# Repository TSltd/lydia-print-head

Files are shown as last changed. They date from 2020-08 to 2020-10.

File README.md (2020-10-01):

# lydia-print-head

Lydia-v4 as printhead

***brief*** this is part of our work of PP OpenSource contributions, please check our [library](https://library.precious-plastic.org/) or our [main page](https://plastic-hub.com/products/) for more.

This print head is a modification of [Lydia-v4](https://plastic-hub.com/products/lydia-v4.html) and aims at a generic solution for most of it´s components.

**Status** : Confirmed & in progress, ETA Mid. of October

## Todos

* [x] Hopper interface & lead-out -> Daniel
* [x] Motor selection
* [ ] Firmware updates
  + [x] Check TCP stack memory/CPU footprint on the ControllinoMega
* [x] Sensors / Audio, LED feedback (status, etc... )
* [ ] Bonus : test HMI
* [ ] Support [RAPID - ABB robots, but uses customer spec](https://library.e.abb.com/public/688894b98123f87bc1257cc50044e809/Technical%20reference%20manual_RAPID_3HAC16581-1_revJ_en.pdf)

### Todos Frederike@3dtreehouse

* [ ] Gantry mount plate, we need the size and locations of the mount holes. We'd need a test rig here.
* [x] Modbus over TCP seems a better fit after all which gives us CAT5 shielding as well some standard connectivity. RS485 has no real standard plugs, ...
* [ ] Location and size of the cabinet, what on the control panel (controls & plugs) ?
* [ ] We have to know how we share power source & ground among all digital circuits. Currently we're mostly at 24V and we need another source for 12V (fans, etc...)
* [ ] Clarify RAPID ethernet connectivity

### Todos TimberStar

* [x] we need a laser cut barrel shield which holds the insulation material
* [x] on the barrel tip, we need some mounting possibilties for fans which are a little heavy as well

## Components

* [x] [OMRON MX2 VFD](https://industrial.omron.es/es/products/3G3MX2-A2022-E) [BOM](https://es.wiautomation.com/omron/variadores-motores-proteccion-de-circuitos/3G3MX2A2022E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)
* [x] Controllino - Mega as already mentioned a few times, adds 280 Euro
* [x] a better motor and gearbox - MotoVario
* [ ] custom firmware development
* [x] ModBus capable PID controllers (3x) : [Omron - E5DC-B](https://industrial.omron.eu/en/products/E5DC-QX2ASM-002) - Din - Rail Module [BOM](https://es.wiautomation.com/omron/plc-sistemas/E5DCQX2ASM002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)
* [Hopper - Linear Solenoid](https://uk.farnell.com/guardian-electric/t12x19-c-24d/solenoid-pull-operation-24vdc/dp/1608128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)

### Noah OS Variant

* [x] [PLC/Proxy for Aux, Sensors, Relays, etc... - CP1L-EM40DT1-D](http://www.ia.omron.com/products/family/1916/lineup.html), works well with [Omron NB NB3Q-TW01B](https://es.wiautomation.com/omron/hmi-pc-industriales/NB3QTW01B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)

# Status

* [Firmware](https://github.com/plastic-hub/hydra), in development but mostly done
* Hardware, in re-design

### Specs

* Voltage : 220V|380V
* Max. 120Kg, first rev. might be around 60KG
* Controller cable length around 20 meter
* PID : +/- 5 degc tolerance, alarm/cooling outputs

### Gantry Mount

* the gantry mount should be detached from the head-mount -> adapter plate
* @todo : run static tests
* the tool flange is on p30, ([see also ATI Toolchanger - YuTu](https://www.youtube.com/watch?v=kDP-oofDn4w&feature=youtu.be))

### Firmware

- [-] For now, we base all on Arduino based and existing PlasticHub firmware framework, in particular we will use [Controllino-Mega](https://www.controllino.biz/product/controllino-mega/) which gives us Ethernet and RS485. The board has been proven reliable and robust (ideal for prototyping).
- [-] VFD and PID control is mapped to Serial communication which might accept G-Code
- [x] VFD will be Omron-M2X series since we can use existing code. The VFD also supports Modbus (rather difficult)
- [ ] Internal registers/coils (custom PlasticHub Firmware) to Modbus rep

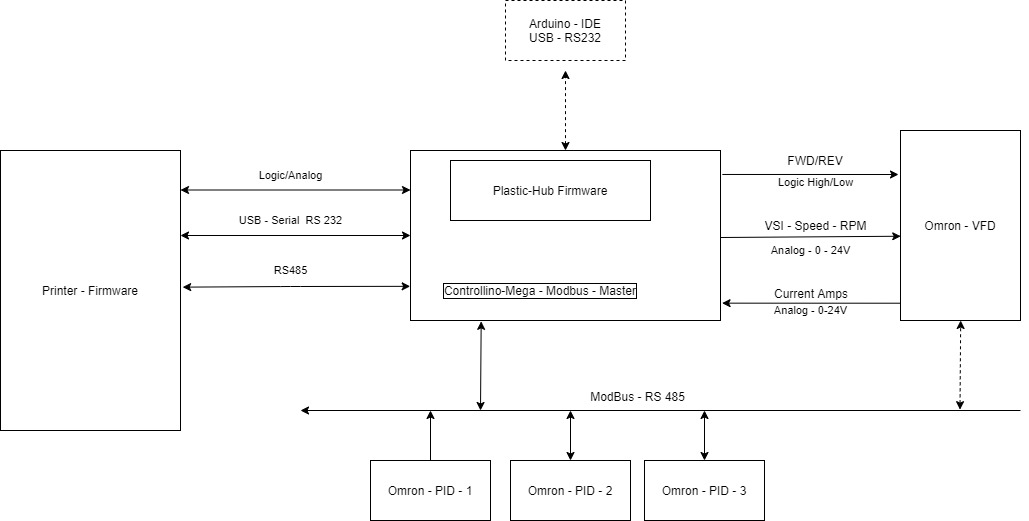
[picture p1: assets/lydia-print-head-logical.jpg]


**[Diagram source](https://app.diagrams.net/#G1L7Prviy9U-2gpcZHm8Z5dj39gxDHd_V_)**

### PID Controller

* [ ] We should go for [Omron E5-C](https://assets.omron.com/m/6f7cd0d93654a7a4/original/E5_C-Temperature-Controller-to-NB-Screen-Template-Tech-Guide.pdf) series which come with Modbus (consider EMI and cable length to the main controller)
* [ ] Each PID will be exposed on the internal ModBus mapping
* There is currently a [custom PID controller](https://github.com/plastic-hub/pid-controller) in development but as mentioned, it's unlikely that it sees the light before November. However, I can imagine we use sub-routines as they're avaiable
* [ ] We should create logging module as well a an API to set temperature profiles for different materials. The logging module will help analyzing different PID settings as well experimenting with barrel cooling (when overshooting becomes an issue).
* [ ] Additional, we forward alarms for overshooting on the internal bus

* **Changes** :  Turns out that the [E5DC / E5DC-B](http://www.ia.omron.com/products/family/3242/) family is better choice.

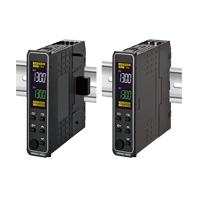
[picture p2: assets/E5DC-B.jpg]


### Barrel

* easy to shorten
* OD should be standard to EU heatbands
* Between Nozzel and barrel we might have some adaptery to exchange different screw tips, up to 10 cm
* should have a mount near the nozzle
* Barrel - motor flange should have some redunancy to enable different barrels

----

### Hopper interface and Hopper

* [-] Feed control ? -> waiting for the robot pictures
* [x] should have a thread interface

## Todos

* [x] Investigate Omron - PID feedback to enable more control via M/G codes (purge, ...)
* [x] Investigate GCode to ROS mapping
* [x] Investigate screw tip machining, if lucky we get away with 4 axis
* [-] Test different VFD/PID checksum/parity settings with larger EMI around

# References

## ROS

* [ROS - Github](https://github.com/ros-industrial)
* [ROS - GBRL - Github](https://github.com/openautomation/ROS-GRBL/wiki/GRBLtron)
* [ROS - Matlab|SimuLnk](https://www.mathworks.com/help/ros/ug/get-started-with-ros-in-simulink.html)
* [ROS Modbus - Wiki](http://wiki.ros.org/modbus)
* [ROS Modbus - PLC - Github](https://github.com/sonyccd/ros_plc_modbus)

## Related Projects

* [Project Noah](https://github.com/plastic-hub/noah)

### Cable robotics

- [The Cable-robot Analysis and Simulation Platform for Research (CASPR)](https://github.com/darwinlau/CASPR)
- [CUHK C3 Robotics Laboratory - Youtube](https://www.youtube.com/channel/UCxadDa3g1fUarP4ldAECtLQ)

### Rapid - ABB

* [Language specs and docs](./vendor/abb/2CSG445026D0201-ANR-LAN-Modbus-TCP-Protocol.pdf)
* [ABB - AC_800M - Protocols](./vendor/abb/3BSE035982-511_en_AC_800M_5.1_Feature_Pack_Communication_Protocols.pdf)

### ABB 6600

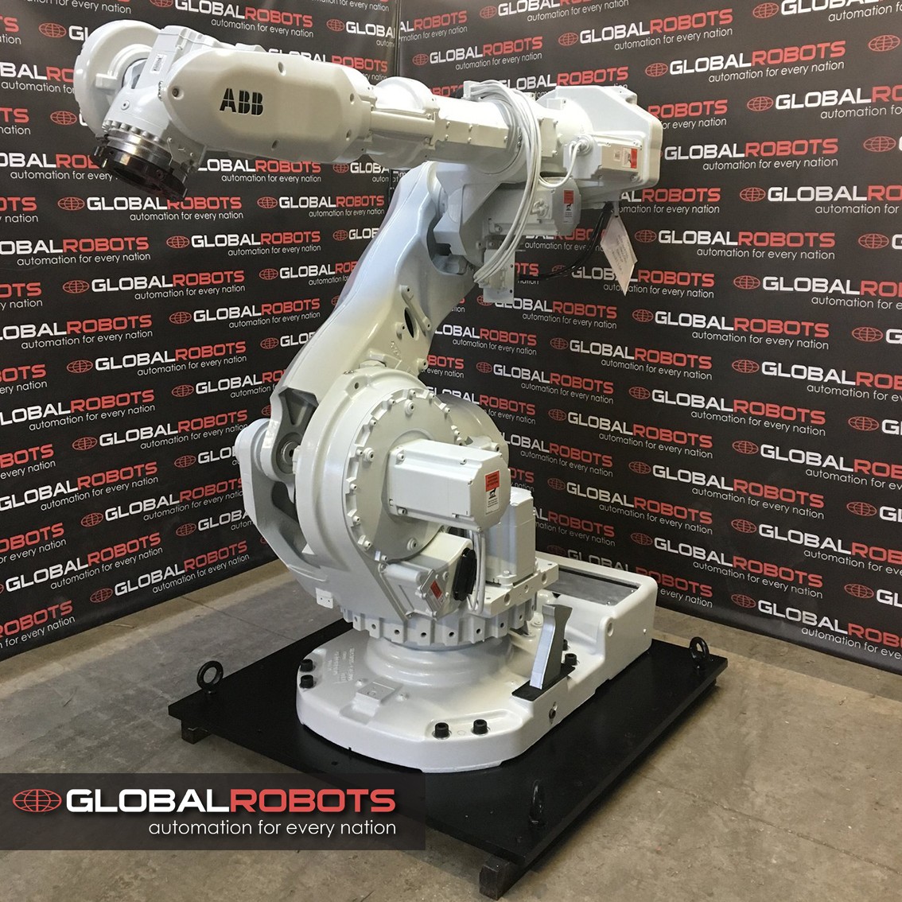
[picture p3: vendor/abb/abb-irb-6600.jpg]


- [ABB - IRC - 5 - Controller](https://new.abb.com/products/robotics/controllers/irc5)
- [ABB - IRC - Datasheet](./vendor/abb/IRC5-Industrial-Robot-Controller-data sheet.PDF)
- [ABB irb 6600 175-2.8](https://library.e.abb.com/public/560fa420555c2d8ac1257b4b0052112c/3HAC023933-001_rev1_en.pdf)
- [ABB irb 6600 175 - 2.8 - Local](./vendor/abb/IRB_6600_R_US 02_05.pdf)
- [ABB 660 - Specs](./vendor/abb/ABB-IR-6600-3HAC14064-1_revH_en_library.pdf)

## Project links

* [Project Slack channel](https://pporgworkspace.slack.com/archives/C01A8G36MRP)
* [Firmware](https://github.com/plastic-hub/hydra)

## Follow ups

- [ ] calc. energy overhead, per printed kg of plastic
- [ ] calc. min. invest to print obvious products
- [ ] investigate possible OS verticals
- [ ] develop generic system & functional design for v2.0 candidats, for 6D robots but also cable driven 3D systems

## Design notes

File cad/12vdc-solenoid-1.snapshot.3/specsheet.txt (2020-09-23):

Model No. T12x13-C-12

Duty Cycle Continuous

'On' Time 100 %

Volts 12 VDC

Resistance 22.8 Ω

Power 6.6 W

Total Weight 10.2 oz

Plunger Weight 1.6 oz

Holding Force 188 oz

UL Recognition Recognized under the component recognition program of Underwriters Laboratories, Inc.

RoHS These parts comply with RoHS directive 2002/95/EC

Current 526 mA

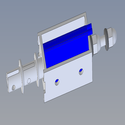
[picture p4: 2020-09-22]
cad/new_barrel_mount/Solenoid+0530+Type/images/large_thumb_Screenshot_2019-12-09_18.55.14.PNG

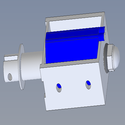
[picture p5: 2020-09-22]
cad/new_barrel_mount/Solenoid+0530+Type/images/large_thumb_Screenshot_2019-12-09_18.54.25.PNG

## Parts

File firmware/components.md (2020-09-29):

## Controllino - Mega

- [Unit Testing](https://docs.platformio.org/en/latest/plus/unit-testing.html?utm_medium=piohome&utm_source=platformio)
- Semiphores : emulated, via ASM noops
- Memory: seems stable with modbus over ethernet

### Omron MX2

- [Programmer](./firmware/OmronMx2.cpp#L460)

### Omron - E5DC

### Calibration

- [TC calibration](https://www.tcdirect.co.uk/product_2_133_21#133/21/1)

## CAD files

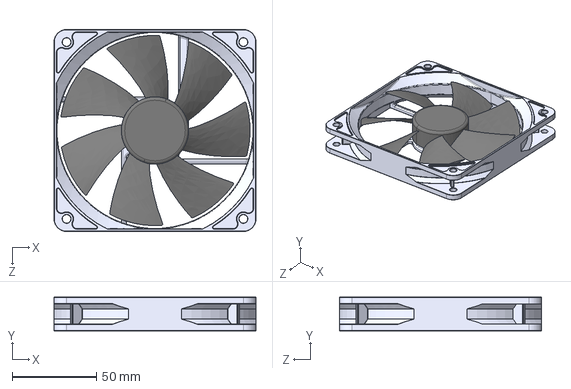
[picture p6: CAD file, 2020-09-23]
cad/fan head/Fan_Assembly.STEP
120.0 x 20.0 x 120.0 mm
Fan_Case
Fan

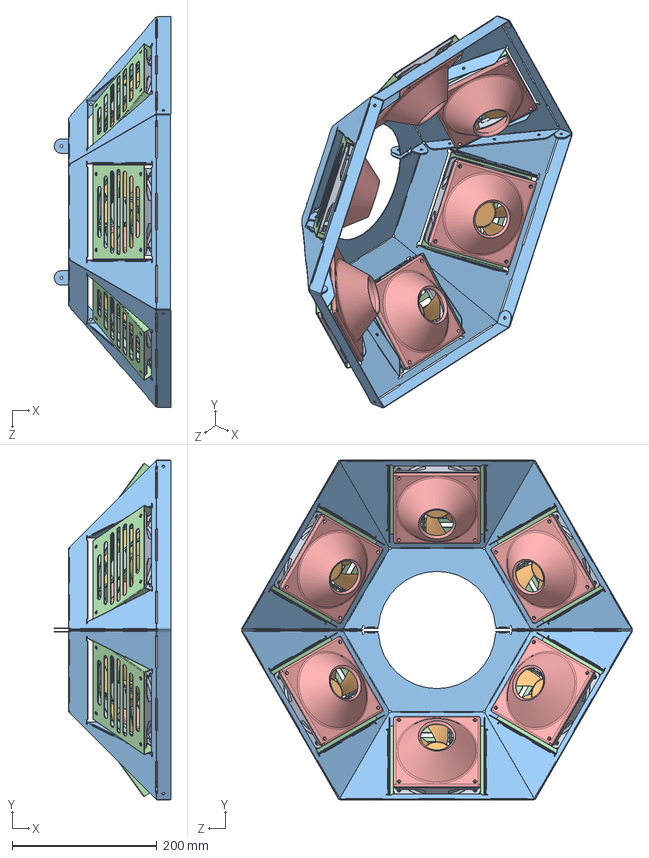
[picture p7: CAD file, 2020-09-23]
cad/new_barrel_mount/fan shroud assembly.SLDASM
161.3 x 469.4 x 540.3 mm
Fan_Case_1 x 6
Fan_1 x 6
fan shroud x 2
fan mount swivel plate x 6
fan nozzle 3d printed x 6

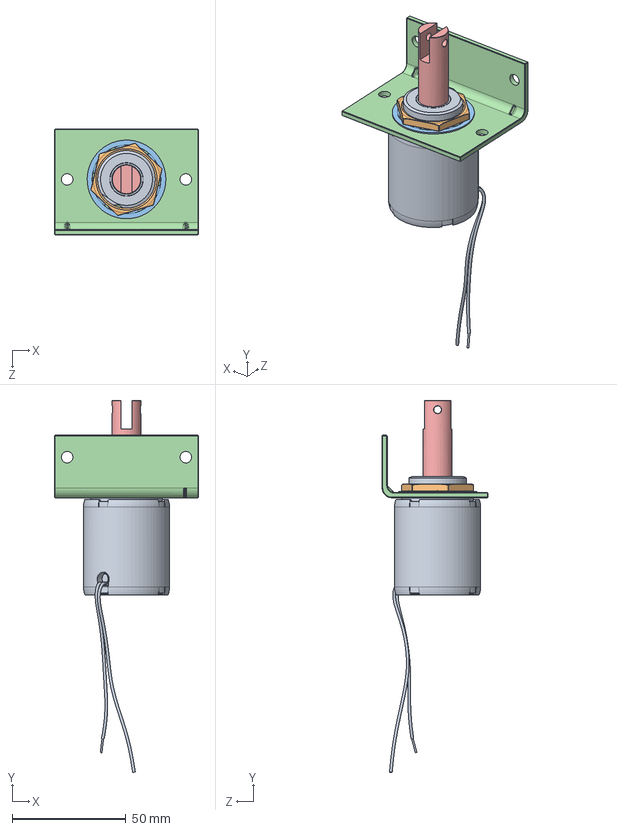
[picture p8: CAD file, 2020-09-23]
cad/12vdc-solenoid-1.snapshot.3/solenoid1.SLDASM
63.5 x 163.7 x 46.6 mm
solenoid body
solenoid nut
washer
bracket
solenoid pin

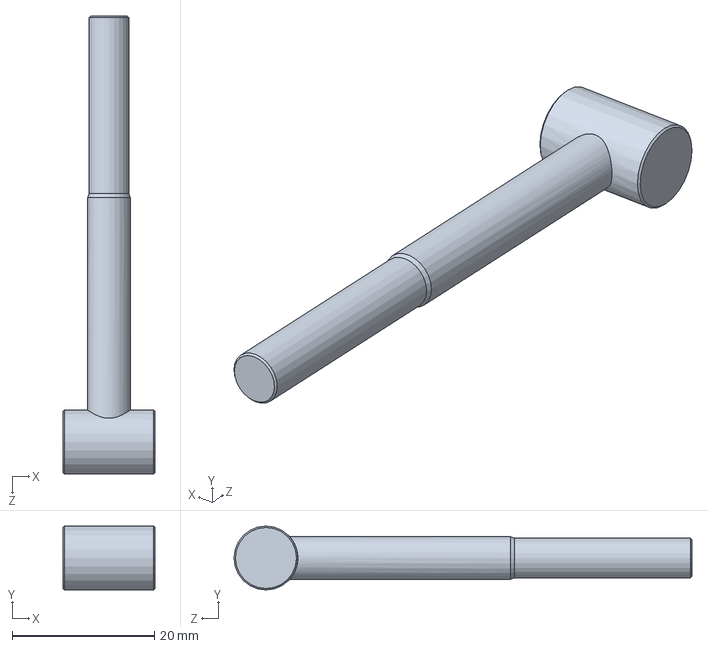
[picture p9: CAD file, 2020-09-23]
cad/quick-release-for-saddle-clamp-1.snapshot.1/Quick Release assembly.SLDASM
13.0 x 9.00 x 64.5 mm

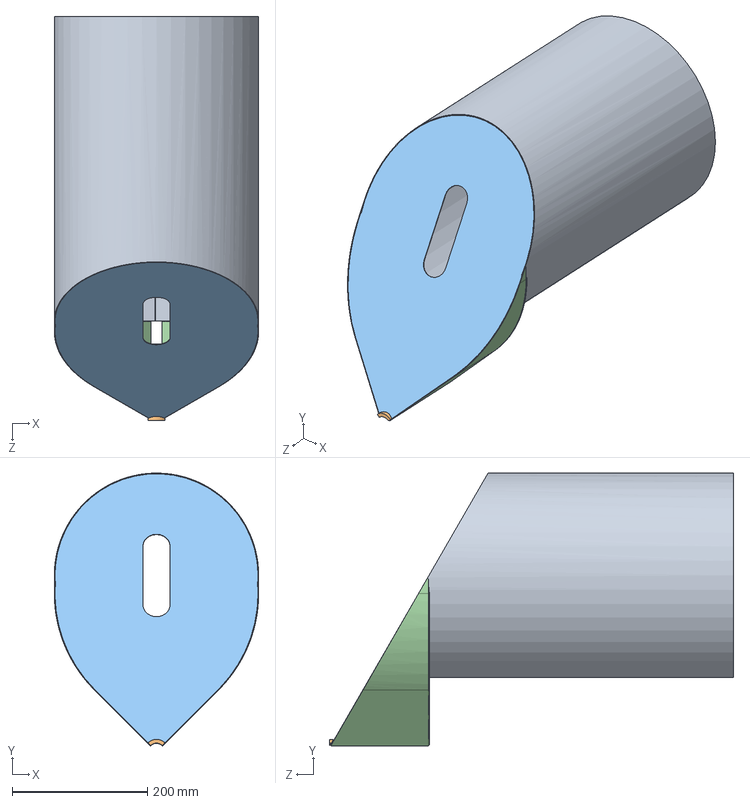
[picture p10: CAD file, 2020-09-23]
cad/new_barrel_mount/Hopper 3 assmebly.SLDASM
302.0 x 403.2 x 597.0 mm
hopper barrel lip
hopper 3 bottom
hopper 3 hopper mouth top and sides

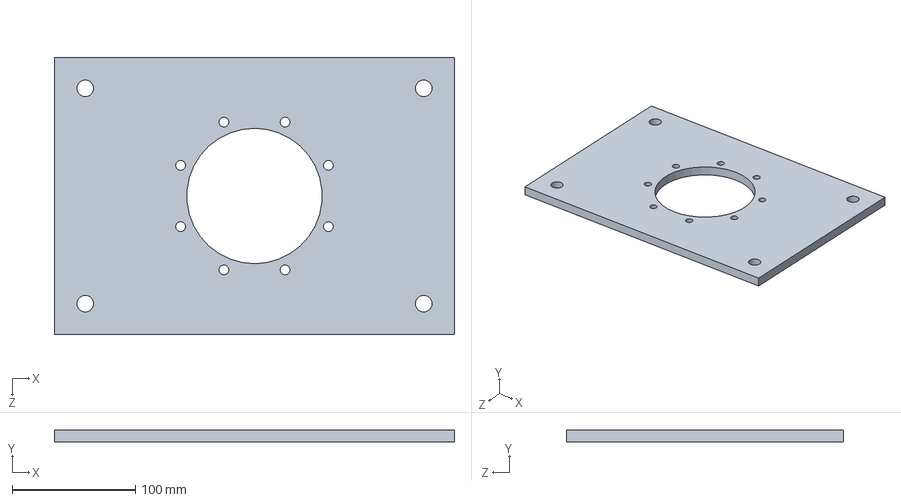
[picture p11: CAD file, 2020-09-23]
cad/main mounting plate new.SLDPRT
325.0 x 10.0 x 225.0 mm

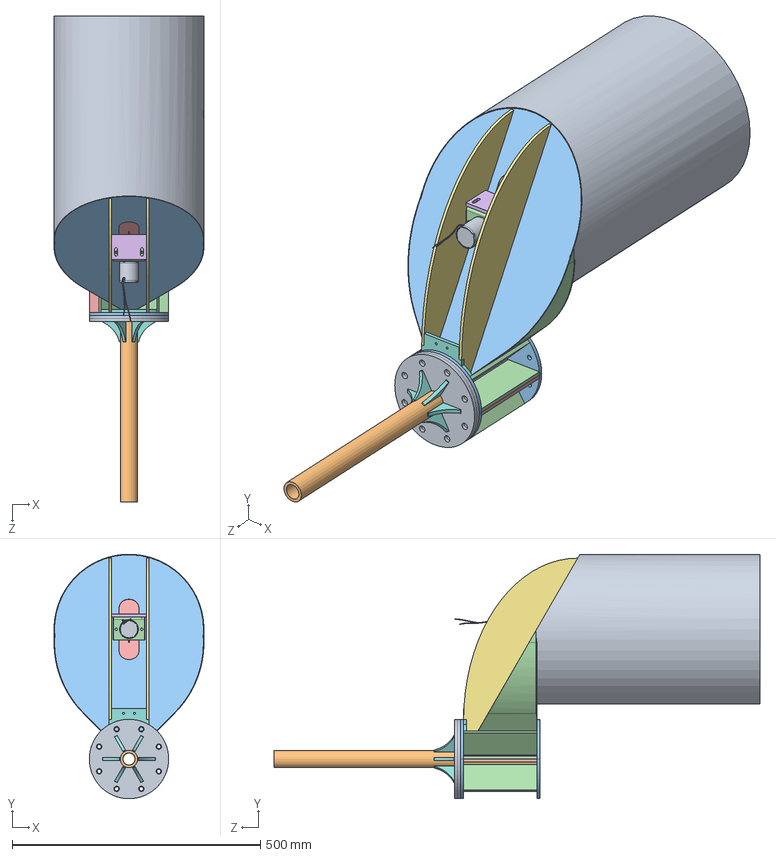
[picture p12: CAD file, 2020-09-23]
cad/new_barrel_mount/subglobal aseembly.SLDASM
302.0 x 492.4 x 979.0 mm
barrel flange new x 2
Barrel 34x25x530 flange version
rectangular half flange x 4
barrel mount hopper flange x 6
Mirrorbarrel mount hopper flange x 2
half barrel section with hole x 2
half barrel section
fin x 6
hopper 3
hopper barrel lip
hopper 3 bottom
hopper 3 hopper mouth top and sides
hopper 3 shaker plate
shakerplate mounting eye
solenoid mount x 2
hopper base flange
solenoid body
solenoid nut
washer
bracket
solenoid pin
solenoid mount plate

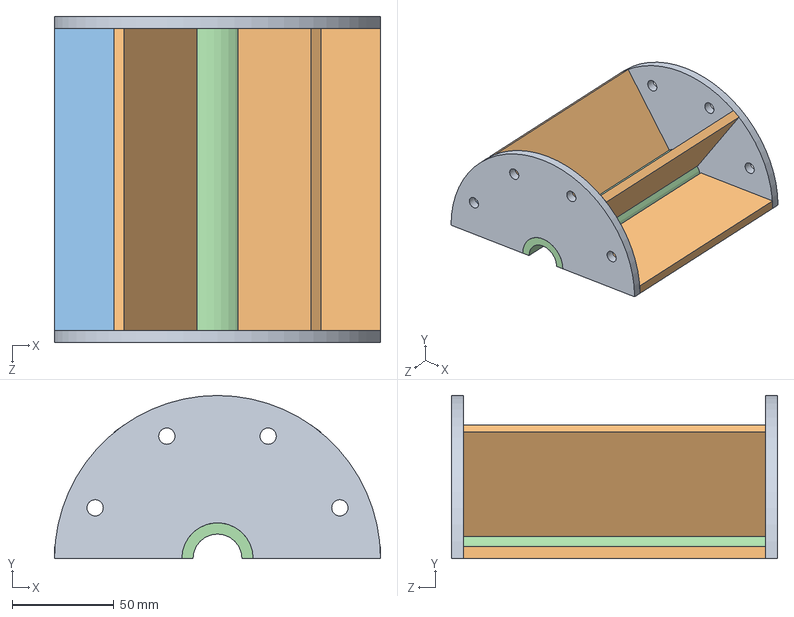
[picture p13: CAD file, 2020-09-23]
cad/new_barrel_mount/hopper base mount assemblyu.SLDASM
160.0 x 80.0 x 160.0 mm
rectangular half flange x 2
barrel mount hopper flange x 3
Mirrorbarrel mount hopper flange
half barrel section

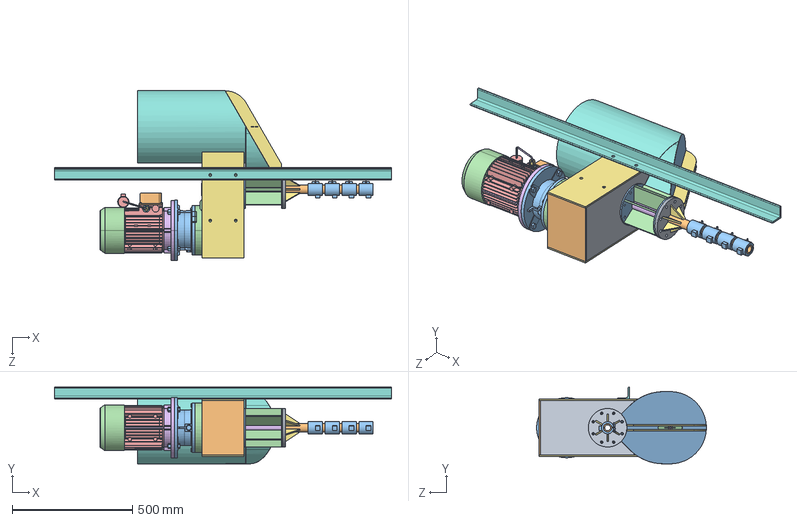
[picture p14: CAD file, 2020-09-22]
cad/Printhead Global Assembly.SLDASM
1400.0 x 318.5 x 705.4 mm
S082C7_3400100_112_B54000NO______________3
S082C7_3400100_112_B54000NO______________5
S082C7_3400100_112_B54000NO______________7
S082C7_3400100_112_B54000NO______________9
S100100LA4IC411B525028X60NO____A004_STD1_3
S100100LA4IC411B525028X60NO____A004_STD1_5
S100100LA4IC411B525028X60NO____A004_STD1_7
S100100LA4IC411B525028X60NO____A004_STD1_9
S100100LA4IC411B525028X60NO____A004_STD1_11
S100100LA4IC411B525028X60NO____A004_STD1_13
S100100LA4IC411B525028X60NO____A004_STD1_15
S100100LA4IC411B525028X60NO____A004_STD1_19
S100100LA4IC411B525028X60NO____A004_STD1_21
S100100LA4IC411B525028X60NO____A004_STD1_23
mount sidepanel x 2
barrel flange new x 2
Barrel 34x25x530 flange version
rectangular half flange x 4
barrel mount hopper flange x 8
half barrel section with hole x 2
half barrel section
fin x 6
hopper 3
hopper chute top
hopper barrel lip
hopper 3 bottom
hopper 3 shaker plate
carcasa
nucleo
bobinado
tapa carcasa
vastago
arandela
tuerca
goma
muelle
shakerplate mounting eye
solenoid mount x 2
hopper base flange
main mounting plate
main mount back plate
Heater_band x 4

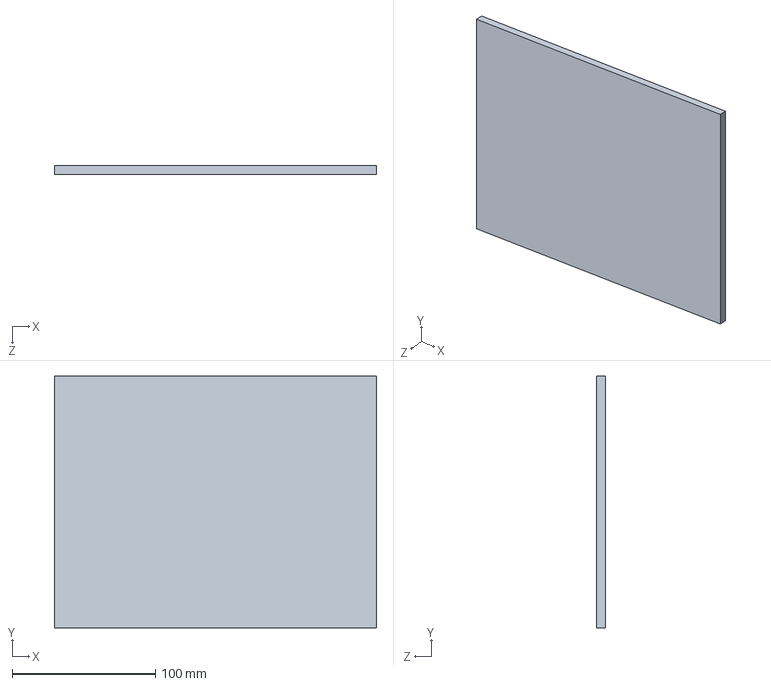
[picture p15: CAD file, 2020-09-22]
cad/main mount back plate.SLDPRT
225.0 x 176.0 x 6.00 mm

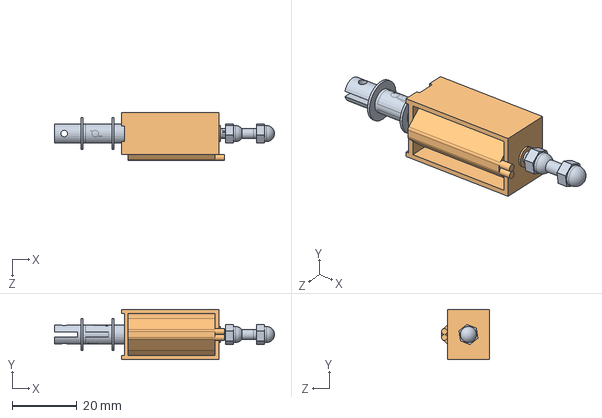
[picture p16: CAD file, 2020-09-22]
cad/new_barrel_mount/Solenoid_0530.SLDASM
68.1 x 15.5 x 14.8 mm
Imported x 2
Imported_2

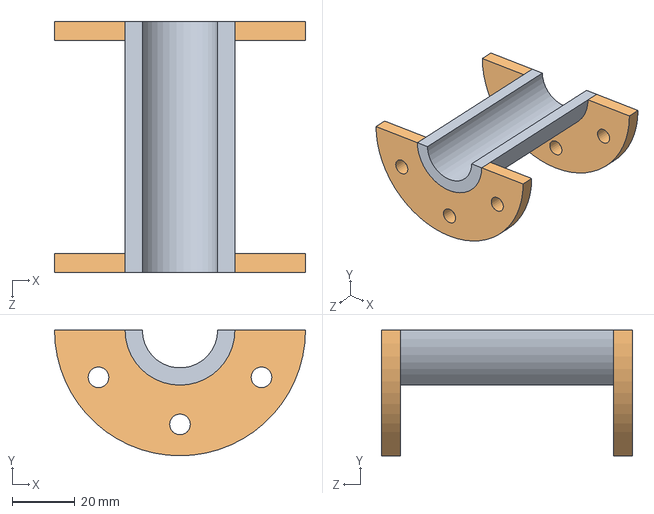
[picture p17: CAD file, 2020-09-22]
cad/new_barrel_mount/barrel mount assembly.SLDASM
80.0 x 40.0 x 80.0 mm
half barrel section
half flange 80x35 60mmboltcirc m6 x 2

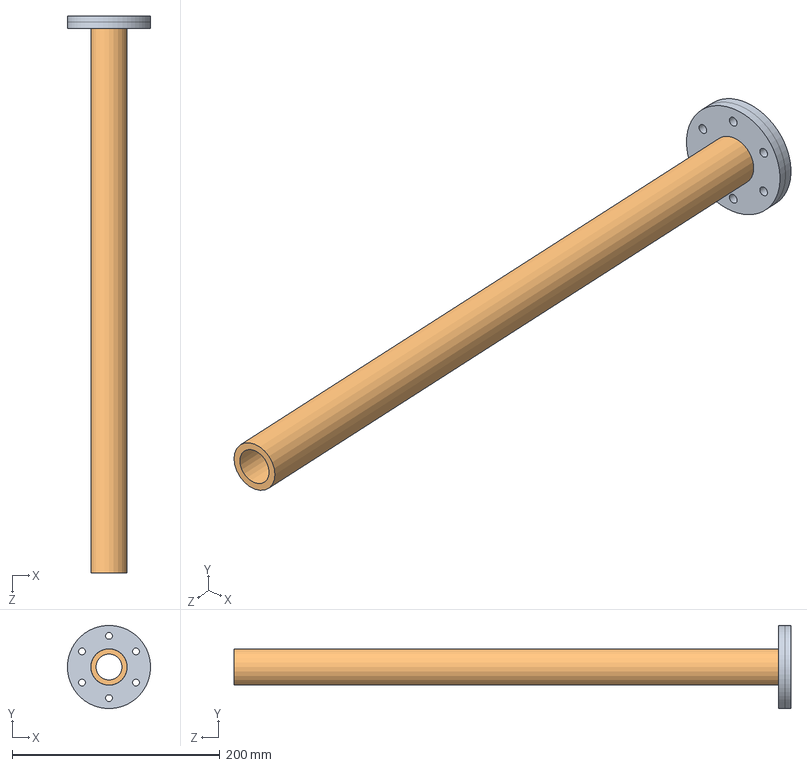
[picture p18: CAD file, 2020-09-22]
cad/new_barrel_mount/flanged barrel and hopper assembly new.SLDASM
80.0 x 80.0 x 536.0 mm
barrel flange new x 2
Barrel 34x25x530 flange version

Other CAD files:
cad/fan head/Fan_Assemblyok.SLDASM
cad/S082C7_3400100_112_B54000NO_____________.sldasm
cad/main mounting plate.SLDPRT
cad/new_barrel_mount/hopper mount assemblyu.SLDASM
cad/new_barrel_mount/Mirrorhopper mount assemblyu.SLDASM
cad/12vdc-solenoid-1.snapshot.3/bracket.sldprt
cad/12vdc-solenoid-1.snapshot.3/inventor/bracket.ipt
cad/12vdc-solenoid-1.snapshot.3/inventor/solenoid body.ipt
cad/12vdc-solenoid-1.snapshot.3/inventor/solenoid nut.ipt
cad/12vdc-solenoid-1.snapshot.3/inventor/solenoid pin.ipt
cad/12vdc-solenoid-1.snapshot.3/inventor/solenoid.iam
cad/12vdc-solenoid-1.snapshot.3/inventor/washer.ipt
cad/12vdc-solenoid-1.snapshot.3/solenoid body.sldprt
cad/12vdc-solenoid-1.snapshot.3/solenoid nut.sldprt
cad/12vdc-solenoid-1.snapshot.3/solenoid pin.sldprt
cad/12vdc-solenoid-1.snapshot.3/solenoid.igs
cad/12vdc-solenoid-1.snapshot.3/solenoid.stp
cad/12vdc-solenoid-1.snapshot.3/washer.sldprt
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

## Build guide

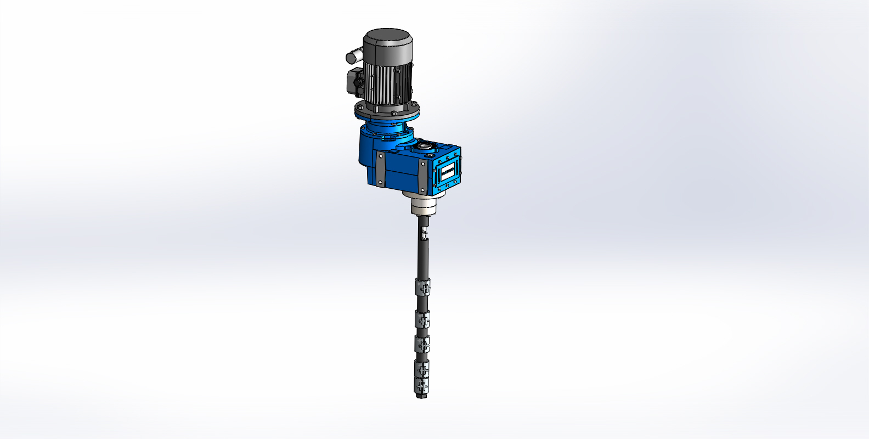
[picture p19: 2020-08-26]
assets/motovario_setup.JPG

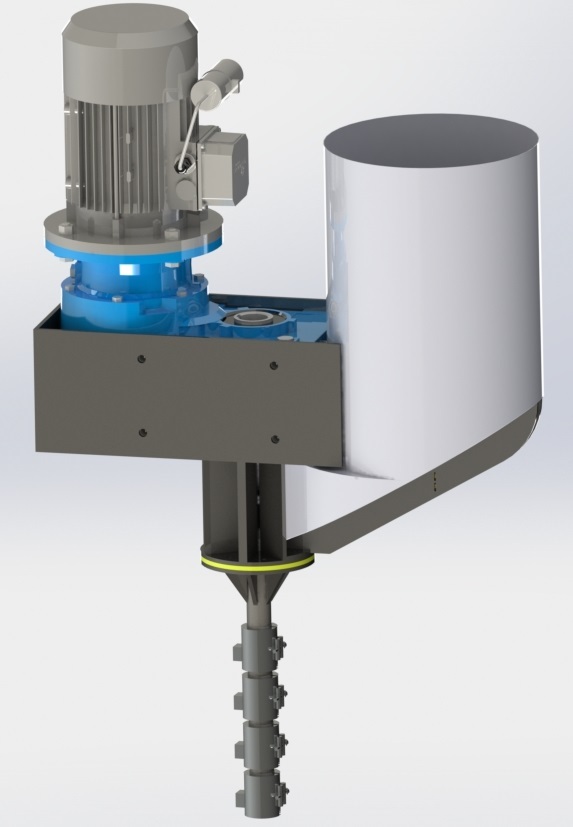
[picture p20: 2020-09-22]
renderings/printhead_work_in_progress.jpg

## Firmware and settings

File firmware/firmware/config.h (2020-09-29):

#ifndef CONFIG_H
#define CONFIG_H

#include "enums.h"
#include "common/macros.h"
#include <Controllino.h>
//////////////////////////////////////////////////////////////////////////////////////////////////////////////////////////////////////////////////
//
//    Core settings
//

#define LOOP_DELAY              500         // Our frame time, exluding delays in some places
#define BOOT_DELAY              1000        // Wait at least this amount in ms after boot before doing anything

// Please consider to set this to false for production - especially with the full feature set since this is requiring extra
// time for the serial communication and will affect the overall framerate/performance
// #define DEBUG true

#define DEBUG_INTERVAL          1000
#define DEBUG_BAUD_RATE         19200       // Serial port speed

#define RELAY_ON 0                          // The relay bank's on value (eg: normally closed) 
#define RELAY_OFF 255                       // The relay bank's off value (eg: normally closed) 

#define DIR_SWITCH_UP_PIN       8           // The 3 position's up output
#define DIR_SWITCH_DOWN_PIN     9           // The 3 position's down output
// #define IGNORE_FIRST_DIRECTION              // Uncomment to ignore the 3pos switch (forward/reverse) after booting. This prevents surprises but possibly also accidents.
//#define DIR_SWITCH_DELAY        500      // If defined, add this as blocking delay between direction changes. Needed for some types of relays.

//////////////////////////////////////////////////////////////////////////////////////////////////////////////////////////////////////////////////
//
//    Machine settings
//

#define USE_CONTROLLINO
// Power, if defined, it enables the power addon which currently can control 2 contactors via relay

#define POWER_0 CONTROLLINO_R10 // Primary power circuit
#define POWER_1 CONTROLLINO_R11 // Secondary power circuit

// the relay type, please toggle if needed
#define POWER_NC true

//////////////////////////////////////////////////////////////////////////////////////////////////////////////////////////////////////////////////
//
//    VFD related
//

// #define HAS_MODBUS_BRIDGE

// VFD FWD Pin. This goes into the relay and then into the VFD.
#define FWD_PIN                             CONTROLLINO_R12

// VFD REV Pin. This goes into the relay and then into the VFD.
#define REV_PIN                             CONTROLLINO_R13

// Motor overload pin, if defined, this will be used to detect jamming
// On an OmronM2X, set the output via C21 (for output pin 11) to 03 for 
// 'Overload' (which is set in C41 )
#define MOTOR_LOAD_PIN                      CONTROLLINO_A2

// Some VFDs have an error signal. Consume this to set FATAL state - Not impl.  - uncomment to activate
// #define VFD_ERROR_PIN 13

// Some VFDs have a reset signal. Consume this in case we have a reset button - Not impl.  - uncomment to activate
// #define VFD_RESET_PIN 12

// Many VFDs accept speed regulation between 0 - 10V, uncomment - activate. This makes 
// only sense when a local quick speed dial or a remote operator is present 
// #define VFD_VSI_PIN         A4


// the time needed to boot up the VDF, only used when we control also the power via POWER_0
#define VFD_BOOT_TIME   500

// Some VFDs have outputs for 'run', 'power up'. If uncommented, we use this set the state 'ready' 
#define VFD_UP_PIN      46

//////////////////////////////////////////////////////////////////////////////////////////////////////////////////////////////////////////////////
//
//    Motor related
//
// IR sensor ( LM393 ) used together with a rotary encoder disc - uncomment to activate
// #define HAS_MOTOR_IR_SENSOR
#define IR_PIN 2                            // Arduino has fixed pins for using interrupts, don't change this
#define IR_INTERVAL         500             // Recompute values in this interval
#define IR_TIMEOUT          1600            // Max. delta time between the sensor's on/off. This is used to recognize a jamming
// #define IR_SPEED                            // Calculate also the speed - needed for addons: injection & printer extension - uncomment to activate

// Motor temperature sensor - uncomment to activate. If the TEMPERTURE_MAX has been exceeded, it will stop the motor and goes into fatal mode.
// #define MOTOR_HAS_TEMPERTURE
#define MOTOR_TEMPERTURE_SCK_PIN  5
#define MOTOR_TEMPERTURE_CS_PIN   6
#define MOTOR_TEMPERTURE_SO_PIN   7

#define MOTOR_TEMPERTURE_INTERVAL 1000            // Sensor read interval, MAX6675 wants it over 1000
#define MOTOR_TEMPERTURE_MAX      50              // Max. motor temperature, in C

//////////////////////////////////////////////////////////////////////////////////////////////////////////////////////////////////////////////////
//
//    Extrusion related
//
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

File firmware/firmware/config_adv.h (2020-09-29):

#ifndef CONFIG_ADV_H
#define CONFIG_ADV_H

#ifdef HAS_DIP

#ifdef USE_MEGA
#define DIP_START 30
#else
#ifdef USE_UNO
#error "No Dip support for now"
#endif
#endif // HAS_DIP

#endif

// enable bridge debugging
//#define BRIDGE_DEBUG

////////////////////////////////////////////////////////////////////////////////
//  
//  Auto reverse time settings

// the time used to reverse after jamming
#define AR_REVERSE_TIME                                 2000

// after reversing came to stop, this is the delay 
// before it's forwarding
#define AR_FORWARD_WAIT_TIME                            1000

// after the delay AR_FORWARD_WAIT_TIME, we set the VFD to forward
// by this time, motor / VFD specifc
#define AR_FORWARDING_TIME                              1500


////////////////////////////////////////////////////////////////////////////////
//  
// Power settings

// optional current sensor to validate primary power is there
// #define POWER_CSENSOR_PRIMARY                           CONTROLLINO_A15

// optional current sensor to validate primary power is there
#define POWER_CSENSOR_SECONDARY                         CONTROLLINO_A14

////////////////////////////////////////////////////////////////////////////////
//  
// Shredding cycle timings
//  this times are mainly delays to switch between 
//  different cycle states:
//
//    enum SHRED_STATE
//    {
//        WAITING = 0,
//        INIT = 1,           --> cycle start
//        POWERED = 2,
//        STARTED = 3,
//        HOMED = 4,
//        PLUNGED = 5,
//        SHREDDED = 6,
//        UNPOWERED = 7,
//        DONE = 8,           --> cycle end
//        CANCELLING = 10,
//        JAMMED = 11,          --> auto reverse begin
//        REVERSING = 12,
//        REVERSED = 13,       
//        STOPPING = 14,
//        FORWARDING = 15,
//        CANCELLED = 16
//    }; 

// the time to wait before checking the power status
// if you experiencing weird behavior, please increase this 
// time, there can be spikes when powering and unpowering the VFD
#define SWT_INIT                                        1500

// after the VFD powered up, wait this time to proceed with shredding 
// or start the homing procedure if there is a plunger present
#define SWT_POWERED                                     2500

// the time interval to use for checking whether the plunger is homed
#define SWT_HOMING                                      2500

// the time interval to use for checking whether the plunger is homed
#define SWT_HOMING                                      2500


// after everything is ready, eg:
//  1. powered
//  2. homed (optinal, plunger present)
//  3. vfd is set to forward
// this is the time to wait before we activate the plunger
#define SWT_STARTED                                     2000

// the interval used to check the 'PLUNGED' state (fixed or limit switches) 
#define SWT_PLUNGED                                     2500

// as soon it's plunged - if plunger present - this is the time to wait 
// before it's stops the VFD. this time depends on the plunger distance to
// the shredder blades. in some cases it's good to leave it spinning by exactly
// this time 
#define SWT_UNPOWERED                                   2000

// the interval to use to checking the HOMED state of the plunger after 
// it stopped the shredder; when it reaches the 'homed' state, the shredding cycle
// is complete
#define SWT_SHREDDED 3000

////////////////////////////////////////////////////////////////////////////////
//
//  Plunger settings and timings
//
//  Times are base on observations rather than calculations. Calculating it
//  will affect plunger speed drasitcally even more lower spec boards.

// interval before reading the limit switch
// this setting will affect your plunging speed since analogRead will 
// consume some time and we do have only one thread.
#define LIMIT_SWITCH_INTERVAL                           400

// base speed and use as factor to scale settings to your hardware
#define PLUNGER_BASE_SPEED                              1000

// manual move speed
#define PLUNGER_MOVE_SPEED                              PLUNGER_BASE_SPEED * 450

// homing speed
#define PLUNGER_HOMING_SPEED                            PLUNGER_BASE_SPEED * 200

// retract speed
#define PLUNGER_RETRACT_SPEED                           PLUNGER_BASE_SPEED * 200

// plunge speed
#define PLUNGER_PLUNGE_SPEED                            PLUNGER_BASE_SPEED * 1600

// plunge/homing travel
#define PLUNGE_PLUNG_DISTANCE                           145000

// inverted travel
#define PLUNGE_HOME_DISTANCE                            -PLUNGE_PLUNG_DISTANCE

// retract travel
#define PLUNGER_RETRACE_DISTANCE                        1500

// in case limit switch broke
#define PLUNGE_MAX_MOVE_TIME                            SECS * 12


///     Optional : current monitor for the plunger stepper motor
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

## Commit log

2020-08-22 PID remarks
2020-08-26 pid change
2020-08-31 l4-print-head readme
2020-09-17 printhead CAD
    [Printhead Global Assembly.SLDASM, Printhead_barrel.SLDPRT, Printhead_nozzle.SLDPRT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]
2020-09-18 renderings v0.2
    [Adapter-M45-Werkzeugflansch.dwg, Adapter-M45-Werkzeugflansch.dxf]
2020-09-18 v0.2 CAD
    [Heater_band.SLDPRT, Hopper 3 assmebly.SLDASM, Imported.sldprt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]
2020-09-21 looking for spirituality in Auroville, lol - punks on tour, at least we know where the hard earned patreon money goes, a huge black hole. how about getting some proper shoes ?
2020-09-23 latest: barrel-mount
    [50mm barrel insulation.SLDPRT, Fan.SLDPRT, Fan_1.sldprt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]
2020-09-23 latest: barrel-mount and more
    [Hopper 3 assmebly.SLDASM, MirrorMirrorframe post motor mount front.SLDPRT, Mirrorbarrel shroud.SLDPRT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]
2020-09-29 moved firmware
    [Adapter-M45-Werkzeugflansch.dwg, Adapter-M45-Werkzeugflansch.dxf]
